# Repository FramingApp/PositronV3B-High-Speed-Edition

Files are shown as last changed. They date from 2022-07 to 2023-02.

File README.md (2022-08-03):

<p align="center">
   
</p>

---

# PositronV3**B**

<!-- [Check out our Youtube to see it in action!](https://www.youtube.com/watch?v=X_QLxTVtyng)

![alt text](https://github.com/KRLAYN/PositronV3/blob/main/Media%20and%20logos/Photos%20and%20renders/PV3%20with%20printsA.jpg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) -->

A modified version if the fantastic [PositronV3 Upside Down 3D Printer](https://github.com/KRLAYN/PositronV3).<br />
This version is deigned to be more manufacturable by hobbyists, with improoved performance (infact prints faster).
<br /><br />
**Features**
-  **No Machined Parts**, *except hotend*
-  **No Synchromesh**, *uses kevlar string*
-  Requires only Hand Hools and 3D printer
-  Integrated PSU

<br />

[BOM Link](https://docs.google.com/spreadsheets/d/1i8a5PYKq8QxL8bjgeb9Q3jwmtq4bS95erUoR0jqxsa8/edit?usp=sharing)

<br />

>**Disclaimer**: `Positron V3B` is still under heavy and rapid development, and things **will change**, if you find somthing that could be improoved, either submit a PR or an Issue in this Git page, or contact harryloud#8251 or AudiotroniX#0585 on Discord.

# Licenses



**License usage**: `CC-BY`

If you are manufacturing this 3D printer or a close derivative, please put `KRALYN Design Logo` visibily on your product and designate `KRALYN` as the inventor of this product. You can find the file inside the logos folder.

***All hardware materials and designs provided here are licensed under the [CC-BY-SA-4.0](https://creativecommons.org/licenses/by-sa/4.0/) hardware license.
All documentation, including the Wiki, is under the Creative Commons [CC-BY-SA-4.0](https://creativecommons.org/licenses/by-sa/4.0/) license***.

<div align="center">
Open Licenses
</div>

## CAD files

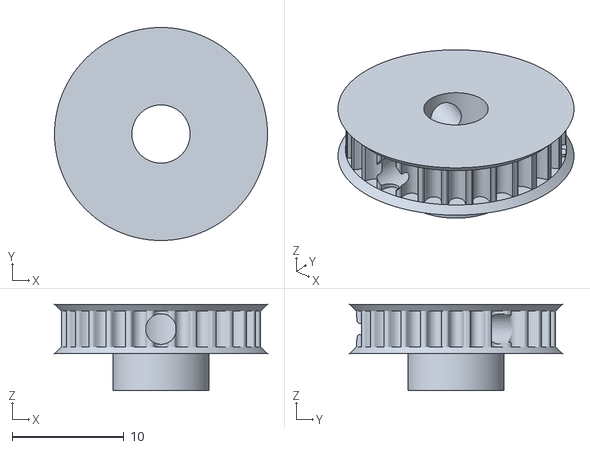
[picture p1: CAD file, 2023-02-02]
CAD files/NX/Pulley_T-MXL-XL-HTD-GT2_N-tooth.stl
19.0 x 19.0 x 7.70

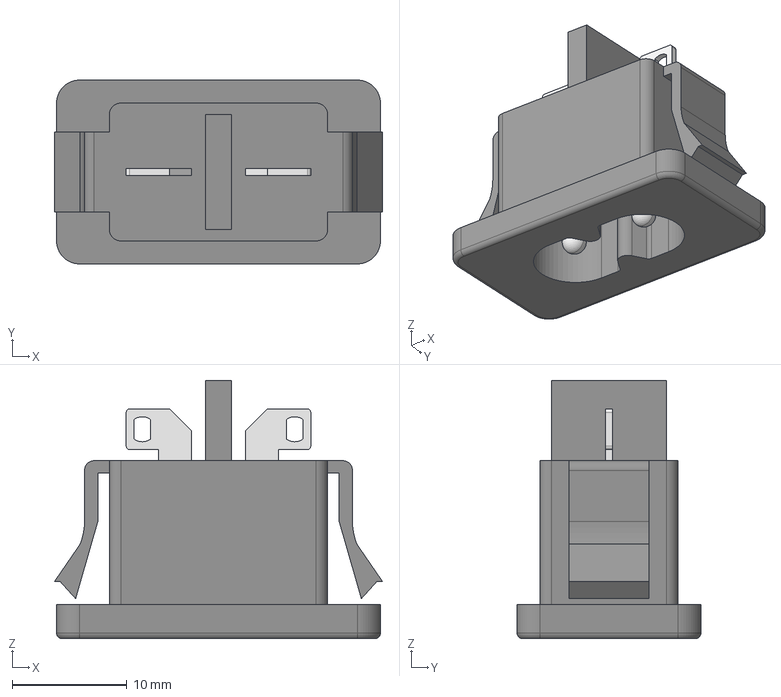
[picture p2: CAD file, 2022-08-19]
CAD files/NX/c7_plug-in.stp
28.6 x 16.0 x 22.5 mm

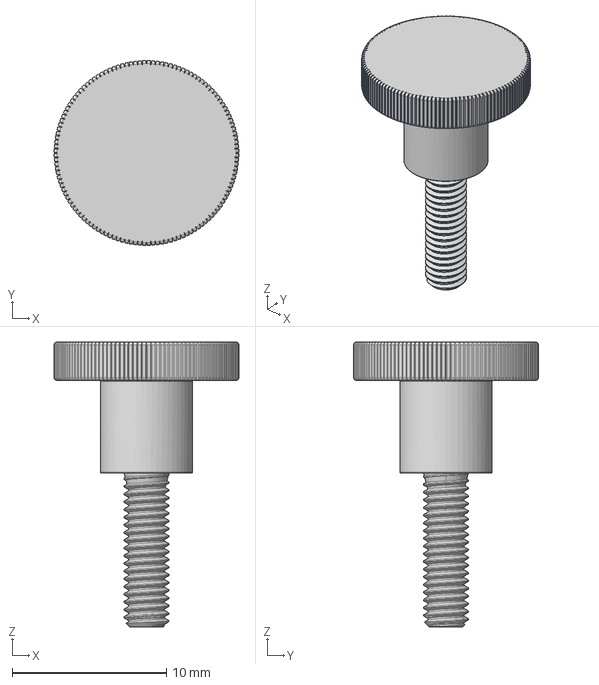
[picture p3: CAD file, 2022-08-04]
CAD files/NX/SKT-M3-10-A1 v1.step
12.0 x 12.0 x 18.5 mm

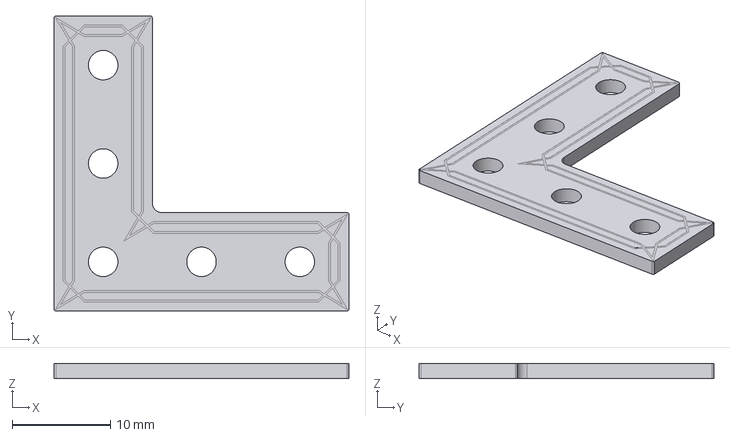
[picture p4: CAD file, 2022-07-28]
CAD files/NX/Makerbeam large right angle stainless bracket.stp
30.0 x 30.0 x 1.50 mm

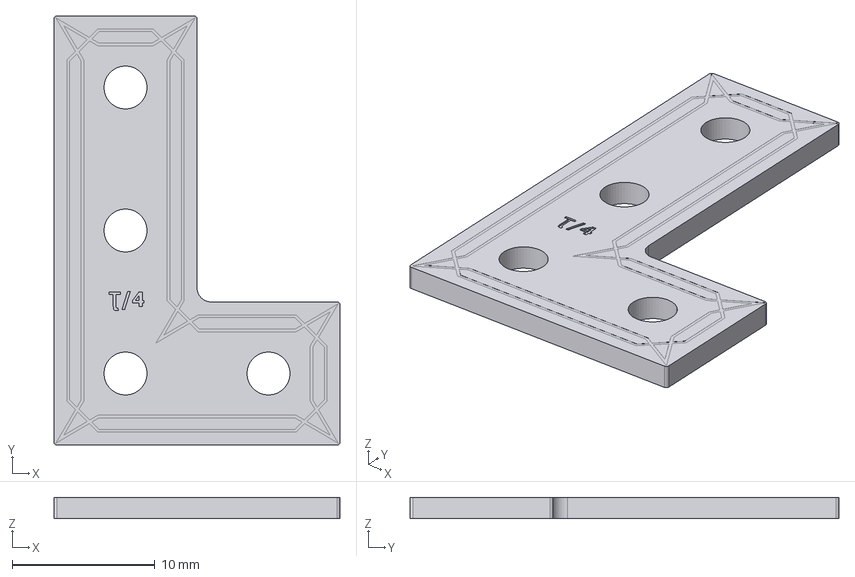
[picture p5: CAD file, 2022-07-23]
CAD files/NX/MakerbeamLBracket-100304.stp
20.0 x 30.0 x 1.50 mm

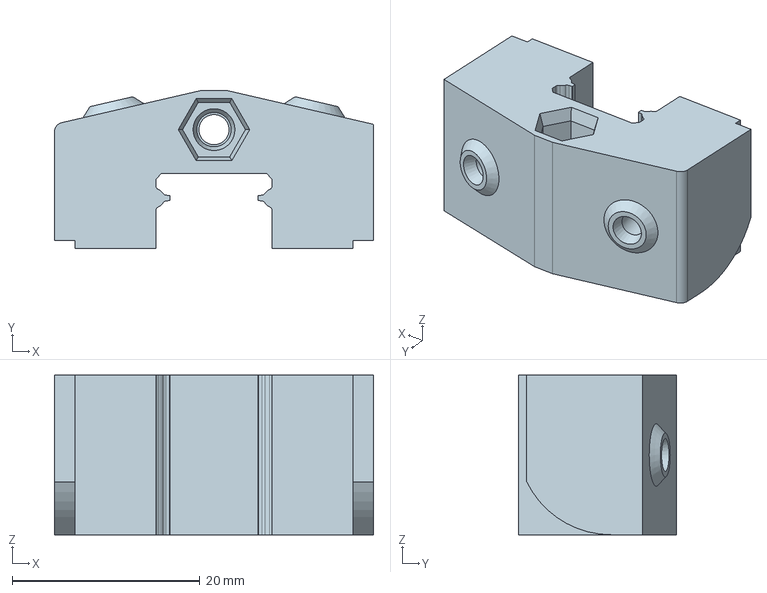
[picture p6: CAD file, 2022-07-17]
CAD files/NX/End Holder Block - Tensioning Mod, 1 part, moving ledges.stp
34.0 x 16.9 x 17.0 mm

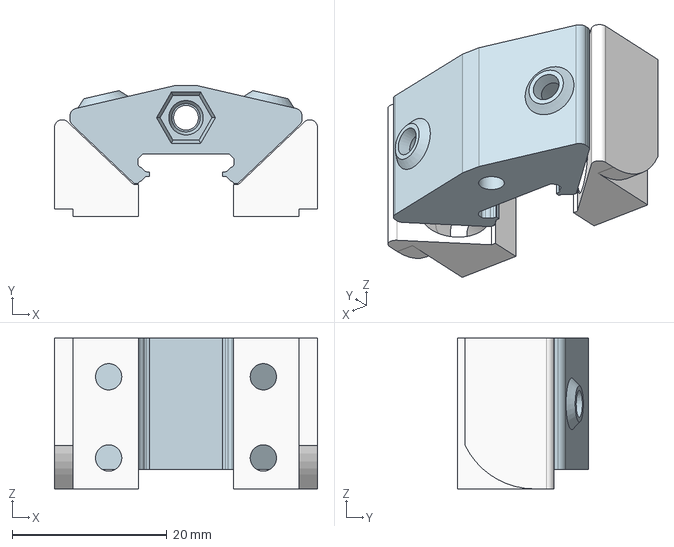
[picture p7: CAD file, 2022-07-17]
CAD files/NX/End Holder Block - Tensioning Mod, Fixed Ledges.stp
34.0 x 17.0 x 19.5 mm

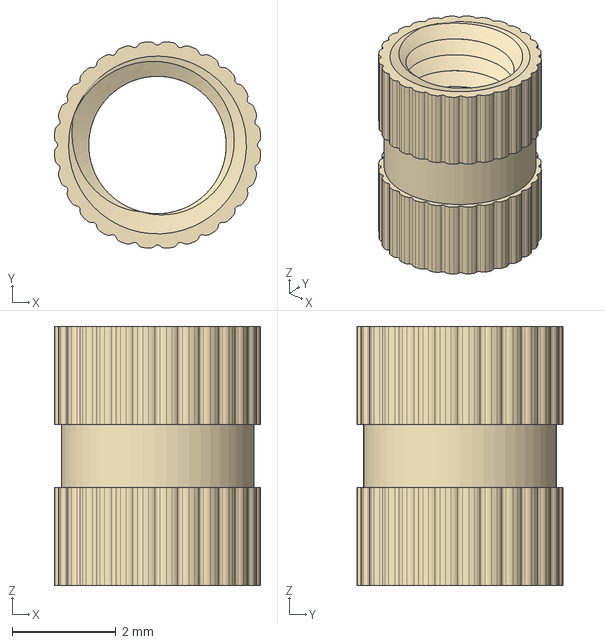
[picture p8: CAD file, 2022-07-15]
CAD files/NX/Threaded Insert - M3x5x4.stp
3.99 x 3.99 x 5.00 mm

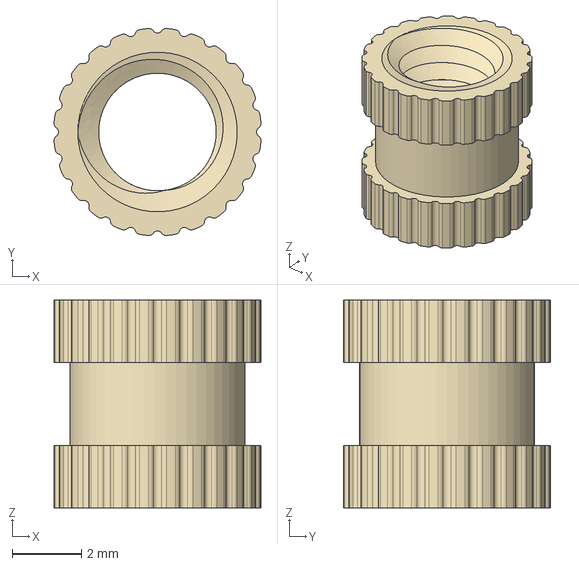
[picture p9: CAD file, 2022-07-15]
CAD files/NX/Threaded Insert - M4x6x6.stp
5.98 x 5.98 x 6.00 mm

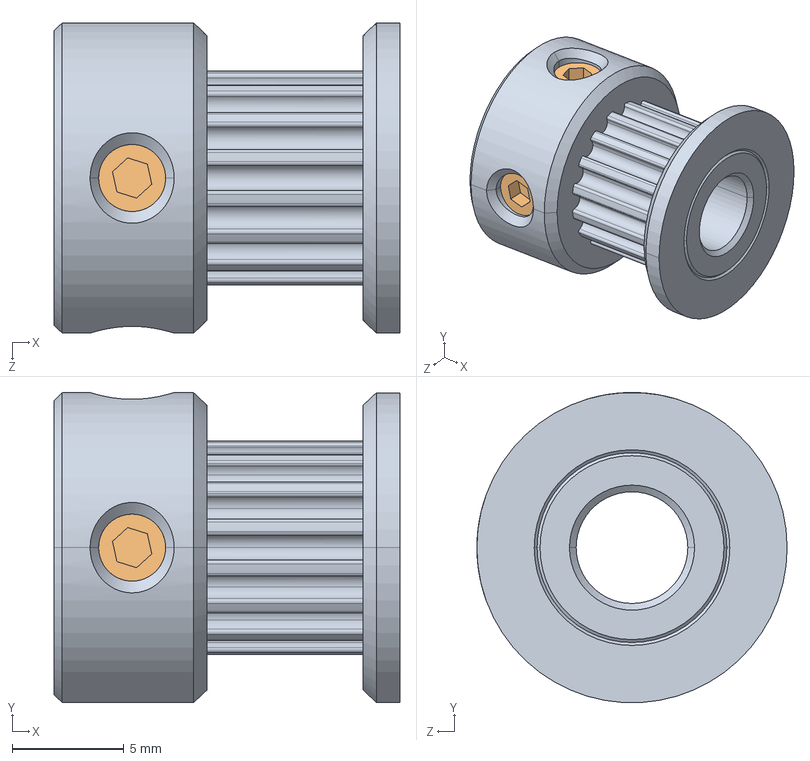
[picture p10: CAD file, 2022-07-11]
CAD files/NX/GT2_16T.STEP
15.5 x 13.9 x 13.9 mm

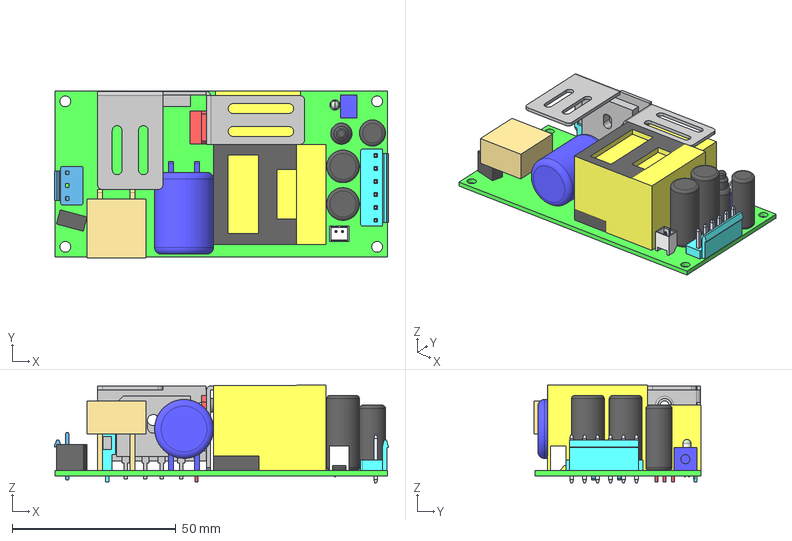
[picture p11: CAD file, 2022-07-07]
CAD files/NX/EPP-200.stp
102.0 x 51.1 x 29.8 mm
PCB
CN1
PIN_CPY
PIN_CPY_CPY
USER_LIBRARY-B5P-VH_PINVH x 6
USER_LIBRARY-B5P-VH_B5P-BODY_WH
C110
p2
pin.1.2.1
C105 x 2
t1
VR
L100
C5
C1
FS2
LED
P110I
BD1
Q1
T2

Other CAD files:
CAD files/NX/Makerbeam_T-Slot_Nut.step
CAD files/NX/Pulley_T-MXL-XL-HTD-GT2_N-tooth.scad
CAD files/1030 extruded aluminum.prt
CAD files/10Pin EXP Male.prt
CAD files/15mm pDia Syncromesh (Mirror).prt
CAD files/19.5mm pDia Syncromesh.prt
CAD files/3 pin 2.54.prt
CAD files/3.5TFT GPIO RPI.prt
CAD files/3.81mm syncromesh 19.81mm gear.prt
CAD files/30mm Fan Mockup 3010 v5.prt
CAD files/37mm 5mm Shaft.prt
CAD files/3D printed toolhead interconnect.prt
CAD files/3x8x15mm Al standoff.prt
CAD files/3x8x15mm Al standoff_1.prt
CAD files/3x8x9.5mm spacers.prt
CAD files/4x12mm Dowel pin.prt
CAD files/5.5mm M3spacors.prt
CAD files/5.5mm m3 Spacros.prt
CAD files/5542481392_step.prt
CAD files/5542484352_step.prt
CAD files/5ohm Polyester Film Heater 10x21cm.prt
CAD files/6 pin megnegtic Pogo Pins.prt
CAD files/6483370560.step_1.prt
CAD files/6483370560.step_2.prt
CAD files/6483370560.step_3.prt
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

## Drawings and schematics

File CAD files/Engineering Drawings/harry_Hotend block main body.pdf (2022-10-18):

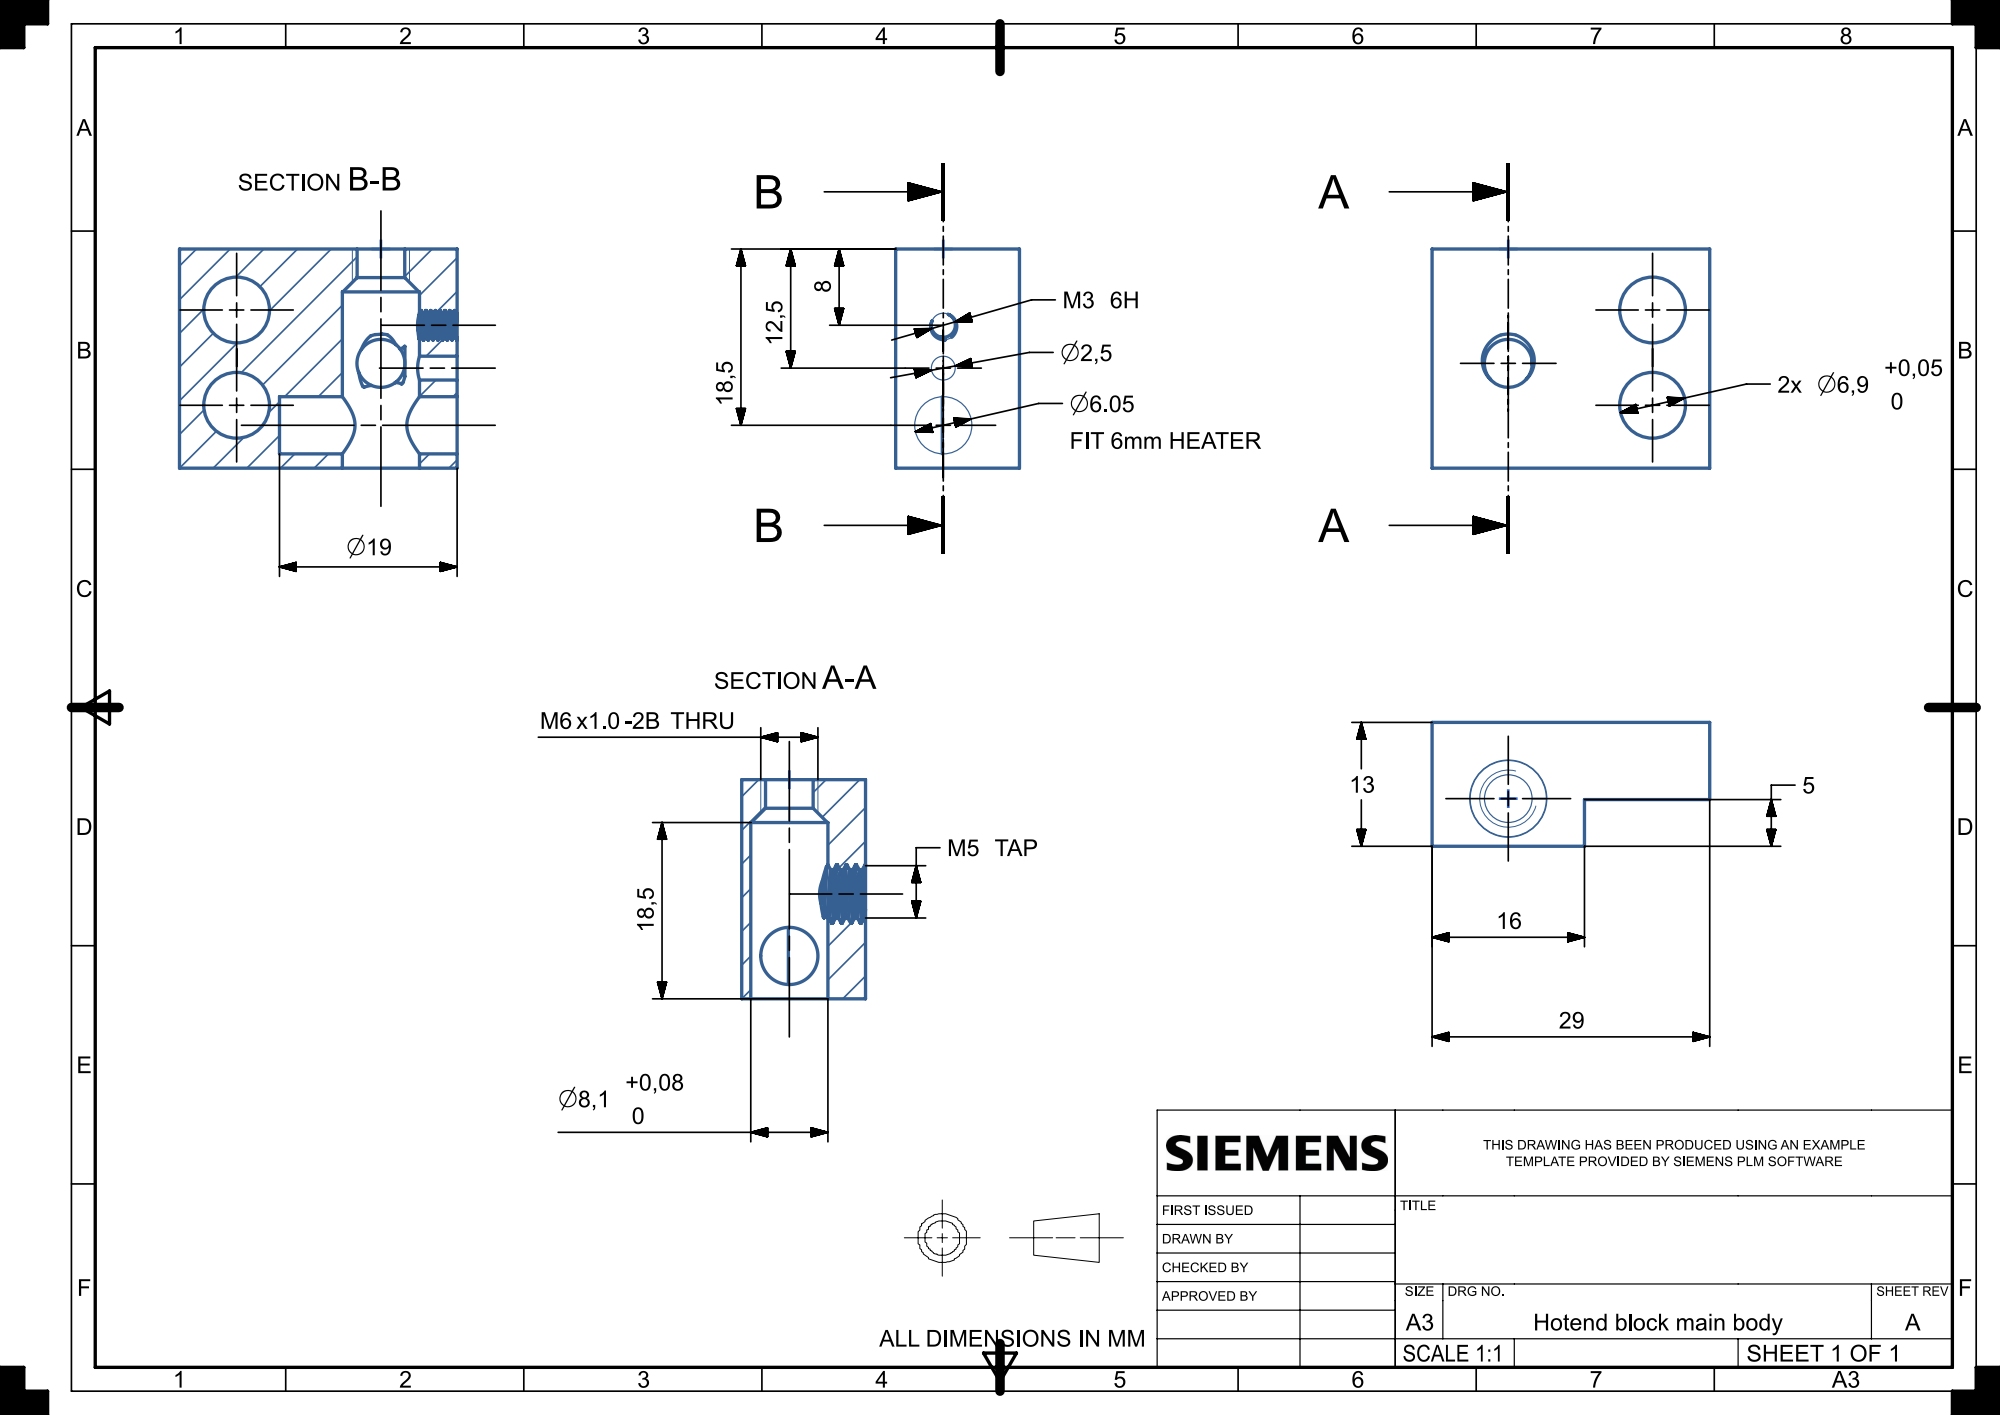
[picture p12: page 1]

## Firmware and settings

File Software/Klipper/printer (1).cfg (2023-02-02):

[printer]
kinematics: corexy
max_velocity: 350
max_accel: 8000
max_accel_to_decel: 7000
square_corner_velocity: 7
max_z_velocity: 7
max_z_accel: 100

[mcu]
serial: /dev/ttyS3
baud: 250000
restart_method: command

[mcu bpi]
serial: /tmp/klipper_host_mcu



[stepper_x] #ST4118X1404-A Motor
step_pin: gpio11
dir_pin: !gpio10
enable_pin: !gpio12
microsteps: 16 #Microsteps were found to improove max speed
rotation_distance: 58.1 #57.1 #set to 60 to run velocity in rpm
#endstop_pin: ^gpio3
endstop_pin: tmc2209_stepper_x:virtual_endstop
homing_retract_dist: 0
position_endstop: 0
position_max: 185
homing_speed: 40
full_steps_per_rotation: 200
step_pulse_duration: 0.000001 #helps with speed a bit
[tmc2209 stepper_x]
interpolate: false
uart_pin: gpio9
tx_pin: gpio8
uart_address: 0 # X = 0, Y = 2
run_current: 1.2 #1.4
#hold_current: 0.7
stealthchop_threshold: 250 #999999
diag_pin: ^gpio4 #x = gpio4, y = gpio3, z = gpio25
driver_SGTHRS: 21

[stepper_y]
step_pin: gpio6
dir_pin: !gpio5
enable_pin: !gpio7
microsteps: 16
rotation_distance: 58.1 #57.1
#endstop_pin: ^gpio4
endstop_pin: tmc2209_stepper_y:virtual_endstop
homing_retract_dist: 0
position_endstop: 0
position_max: 180
homing_speed: 40
full_steps_per_rotation: 200
step_pulse_duration: 0.000001
[tmc2209 stepper_y]
interpolate: false
uart_pin: gpio9
tx_pin: gpio8
uart_address: 2 # X = 0, Y = 2
run_current: 1.2 #1.4
#hold_current: 0.7
stealthchop_threshold: 250 ;999999
diag_pin: ^gpio3 #x = gpio4, y = gpio3, z = gpio25
driver_SGTHRS: 24


[stepper_z]
step_pin: gpio19
dir_pin: gpio28
enable_pin: !gpio2
microsteps: 16
rotation_distance: 4 #lead screw pitch
endstop_pin: probe:z_virtual_endstop
position_min: -2.0
position_max: 181
homing_speed: 12

[tmc2209 stepper_z]
uart_pin: gpio9
tx_pin: gpio8
uart_address: 1
run_current: 0.7
hold_current: 0.4
stealthchop_threshold: 999999

[extruder]
step_pin: gpio14 #gpio19
dir_pin: !gpio13 #gpio28
enable_pin: !gpio15 #!gpio2
microsteps: 16
rotation_distance: 4.92#1.65
nozzle_diameter: 0.6
filament_diameter: 1.75
full_steps_per_rotation: 400 #0.9 deg
heater_pin: gpio23
sensor_type: Generic 3950
sensor_pin: gpio27
control: pid
pid_Kp: 25.12
pid_Ki: 1.073
pid_Kd: 147
min_temp: -100
max_temp: 255
max_extrude_cross_section:2
pressure_advance: 0.18 #0.18
min_extrude_temp: 170
max_extrude_only_distance: 1000

[tmc2209 extruder]
uart_pin: gpio9
tx_pin: gpio8
uart_address: 3 #1
run_current: 0.7#0.69
hold_current: 0.4#0.4
stealthchop_threshold: 999999

[heater_bed]
heater_pin: gpio21
sensor_type: Generic 3950
sensor_pin: gpio26
pwm_cycle_time: 0.3#0.015 #longer as small electric shock when touching ITO. Hurts if high freqency
max_power: 1
control: pid
pid_Kp: 56.852
pid_Ki: 2.1
pid_Kd: 383.75
min_temp: -100
max_temp: 90

[controller_fan mcu_fan]
pin: gpio18
max_power: 1
shutdown_speed: 0
cycle_time: 0.00002
kick_start_time: 1
fan_speed: 1
idle_timeout: 1
stepper: stepper_x, stepper_y#, stepper_z


# [heater_fan nozzle_cooling_fan]
# pin: gpio20
# kick_start_time: 1

[fan]
pin: gpio20#bpi:gpiochip0/gpio17
max_power: 1
cycle_time: 0.001 #https://www.youtube.com/watch?v=E3kBau82SwU&ab_channel=Vez3D
hardware_pwm: false
shutdown_speed: 0
#pin: gpio18
# kick_start_time: 1


[heater_fan extruder_heatsink_fan]
heater: extruder
heater_temp: 50.0
pin: gpio17
max_power: 1
shutdown_speed: 0
cycle_time: 0.00002
# kick_start_time: 1
fan_speed: 1
# idle_timeout: 5






[force_move]
enable_force_move = true

[gcode_macro FORCE_Z_UP]
gcode: FORCE_MOVE STEPPER=stepper_z DISTANCE=30 VELOCITY=40

[virtual_sdcard]
path: ~/gcode_files

[safe_z_home]
home_xy_position: 90,90 #90,90 # Change coordinates to the center of your print bed
speed: 100
z_hop: 3                # Move up 5mm
z_hop_speed: 5

[probe]
pin: ^gpio25 #x = gpio4, y = gpio3, z = gpio25
x_offset: -6
y_offset: -40
#z_offset: 1.5 #0.8
speed: 3
samples: 3
sample_retract_dist: 0.7

[bed_tilt]
points: 
  25,15
  130,15
  130,150
  35,150
speed: 100
horizontal_move_z: 4

[bed_screws]
screw1: 0, 145
screw2: 170, 145
screw3: 100, 0




[gcode_macro UNLOAD_FILAMENT]
gcode = 
  M83 
  G1 E-30 F1800
  G1 E-300 F2500 #880
  # G1 E-100 F1200
  # G1 E-100 F1200
  # G1 E-100 F1200
  G92 E0
  G90

[gcode_macro LOAD_FILAMENT]
gcode = 
  M83 
  G1 E300 F2500 #300
  # G1 E100 F1200
  # G1 E100 F1200
  # G1 E100 F1200
  G1 E20 F600
  G92 E0
  G90
  



[gcode_macro G29]
gcode = 
  G28
  G1 Z5 F800
	BED_TILT_CALIBRATE

[delayed_gcode my_delayed_gcode]
gcode:
    SET_LED LED=WS2812 RED=0 GREEN=0.05 BLUE=0.01 INDEX=3
    SET_LED LED=WS2812 RED=0.1 GREEN=0.1 BLUE=0.05 INDEX=2
    SET_LED LED=WS2812 RED=0.1 GREEN=0.1 BLUE=0.05 INDEX=1
    G4 P100
    SET_LED LED=WS2812 RED=0 GREEN=0.1 BLUE=0.02 INDEX=3
    SET_LED LED=WS2812 RED=0.2 GREEN=0.2 BLUE=0.1 INDEX=2
    SET_LED LED=WS2812 RED=0.2 GREEN=0.2 BLUE=0.1 INDEX=1
    G4 P100
    SET_LED LED=WS2812 RED=0 GREEN=0.15 BLUE=0.04 INDEX=3
    SET_LED LED=WS2812 RED=0.3 GREEN=0.3 BLUE=0.15 INDEX=2
    SET_LED LED=WS2812 RED=0.3 GREEN=0.3 BLUE=0.15 INDEX=1
    G4 P100
    SET_LED LED=WS2812 RED=0 GREEN=0.2 BLUE=0.05 INDEX=3
    SET_LED LED=WS2812 RED=0.4 GREEN=0.4 BLUE=0.2 INDEX=2
    SET_LED LED=WS2812 RED=0.4 GREEN=0.4 BLUE=0.2 INDEX=1
    G4 P100
    SET_LED LED=WS2812 RED=0 GREEN=0.3 BLUE=0.1 INDEX=3
    SET_LED LED=WS2812 RED=0.5 GREEN=0.5 BLUE=0.25 INDEX=2
    SET_LED LED=WS2812 RED=0.5 GREEN=0.5 BLUE=0.25 INDEX=1
    G4 P100
    SET_LED LED=WS2812 RED=0.6 GREEN=0.6 BLUE=0.3 INDEX=2
    SET_LED LED=WS2812 RED=0.6 GREEN=0.6 BLUE=0.3 INDEX=1
    G4 P100
    SET_LED LED=WS2812 RED=0.7 GREEN=0.7 BLUE=0.35 INDEX=2
    SET_LED LED=WS2812 RED=0.7 GREEN=0.7 BLUE=0.35 INDEX=1
    G4 P100
    SET_LED LED=WS2812 RED=0.9 GREEN=0.9 BLUE=0.45 INDEX=2
    SET_LED LED=WS2812 RED=0.9 GREEN=0.9 BLUE=0.45 INDEX=1
initial_duration: 0.1

[pause_resume]

[gcode_macro CANCEL_PRINT]
rename_existing: BASE_CANCEL_PRINT
gcode:
  TURN_OFF_HEATERS
  CLEAR_PAUSE
  SDCARD_RESET_FILE
  G91 E0
  G1 E-1.0 F240
  G92 E0
  G1 X5 Y5 F3000
  G91
  G1 Z25 F800
  G1 Z25 F800
  G1 Z25 F800
  G90

  BASE_CANCEL_PRINT

[gcode_macro RESUME]
rename_existing: BASE_RESUME
gcode:
  ##### read E from pause macro #####
  {% set E = printer["gcode_macro PAUSE"].extrude|float %}
  ##### end of definitions #####
  G91
  G1 E{E} F240
  RESTORE_GCODE_STATE NAME=PAUSE_state
  BASE_RESUME

[gcode_macro PAUSE]
rename_existing: BASE_PAUSE
# change this if you need more or less extrusion
variable_extrude: 1.0
gcode:
  ##### read E from pause macro #####
  {% set E = printer["gcode_macro PAUSE"].extrude|float %}
  ##### set park positon for x and y #####
  # default is your max posion from your printer.cfg
  {% set x_park = printer.toolhead.axis_maximum.x|float - 10.0 %}
  {% set y_park = printer.toolhead.axis_maximum.y|float - 10.0 %}
  ##### calculate save lift position #####
  {% set max_z = printer.toolhead.axis_maximum.z|float %}
  {% set act_z = printer.toolhead.position.z|float %}
  {% if act_z < (max_z - 2.0) %}
      {% set z_safe = 2.0 %}
  {% else %}
      {% set z_safe = max_z - act_z %}
  {% endif %}
  ##### end of definitions #####
  SAVE_GCODE_STATE NAME=PAUSE_state
  BASE_PAUSE
  G91
  G1 E-{E} F240
  G1 Z{z_safe} F900
  G90
  G1 X{x_park} Y{y_park} F5000



[gcode_macro BACK_AND_FORTH_X_TIMES]
gcode: 
  {% set numtimes = params.NUMTIMES|default(1, true)|int %}
  {% set motor_letter = params.MOTOR_LETTER|default("x", true)|string %}
  {% set speed = params.SPEED|default(500, true)|int %}
  {% set accel = params.ACCEL|default(10000, true)|int %}

  {% for i in range(numtimes * 2) %}
    FORCE_MOVE STEPPER=stepper_{ motor_letter } DISTANCE={ "-" if (i%2 == 1) }200 VELOCITY={ speed } ACCEL={ accel } 
  {% endfor %}



[neopixel WS2812]
pin: gpio24
chain_count: 5
color_order: GRB
initial_RED: 0.0
initial_GREEN: 0.0
initial_BLUE: 0.0

[display_status]

#*# <---------------------- SAVE_CONFIG ---------------------->
#*# DO NOT EDIT THIS BLOCK OR BELOW. The contents are auto-generated.
#*#
#*# [bed_tilt]
#*# x_adjust = 0.006243
#*# y_adjust = -0.013471
#*# z_adjust = 0.186993
#*#
#*# [probe]
#*# z_offset = 1.700

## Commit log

2022-05-24 initial pissings about of bldc with a MAD 5005 with 4:1 reduction
    [1030 extruded aluminum.prt, 10Pin EXP Male.prt, 15mm pDia Syncromesh (Mirror).prt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]
2022-05-25 NX: Laoded in a work started on modifying baseplate and integrating components
    [1030 extruded aluminum.prt, 10Pin EXP Male.prt, 15mm pDia Syncromesh (Mirror).prt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]
2022-07-04 Extruder angled to allow the fillament path to go behind the z axis. This eliminates the need to cut a large slot in the z axis.
    The z axis has also been converted to use 10x10 makerbeam extrusions
    [1030 extruded aluminum.prt, AL bracket Extruder Mounting.prt, Extruder Cap.prt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]
2022-07-07 Figuring out layout of motors and boards. Z axis leadscrew currently uses a needle bearing, but probalby move to deep groove beraings
    [03-26000.prt, 06-8_A.prt, 1030 extruded aluminum.prt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]
2022-07-11 Was thinking about using flanged ball bearings, and removable belt from the z axis pulley.
    However it woudl be better to have a spring loaded z motor and captive belt ont eh z pulley adn stow the pulley around the back of the z axis when in storage. ANd move back to needle bearings
    [90 degree Bed Holder.prt, Base Plate.prt, Base plate and Y axis assembly.prt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]
2022-07-15 Z axis block modifed for 3d printing, required a m4 and m3 insert. Also tensions from hte z block now. Much better. I have 3d pritned and tested and appears to work well.
    [90 degree Bed Holder.prt, Base plate and Y axis assembly.prt, MGW 9 Rail v1.prt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]
2022-07-15 Modifed Z axis holder block to use captive nut as m3 insert kept pulling out according to MellonColley's discord testing. Also added supressed modifcation to Z axis block that enables it for use on t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
    [Z axis Holder block.prt]
2022-07-15 Working paarametic Pulley. Collar is designed to fit down, through the motor throat and sit agianst the bearing for perfect height.
    Print at 0.1mm, 100% infil and with a brim or raft if havign trouble printing
    [synchromeshPulleyNXAttempt.prt]
2022-07-17 After Testing of the tnesioning end holder block mod by MelonColley, some updates were done. 1st, it allows the use of either a m3 insert, or a m3 nut. And 2nd, 2 versions have been created. One is a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
    This is not mature and ready for a PR to the main postron repo.
    [End Holder Block - Tensioning Mod, 1 part, moving ledges.stp, End Holder Block - Tensioning Mod, Fixed Ledges.stp, Z axis Holder block.prt]
2022-07-17 Genral Updates, Pulleys modifed for 28mm motors, Bed hodler updated further for 3d printing. Z axis lead screw and top stopper have been printed and tested in real life and small modifications have b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
    [90 degree Bed Holder.prt, Nema 17 28mm.prt, Positron V3.2 Rev B UNFOLEDE v53_step.prt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]
2022-07-23 Lots and lots of improovments from 3d printing testing. Figured out the placement of electronics (PSU Left 2 arrangment). XY Motor active cooling done via 2 fans and a 22x70x6mm SSD heatsink that has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
    Positioning of components, especialy the fan became very diffuclt in the folded position. As such, the printer base may have to be extended by 2mm.
    Might move to 26.5mm E3D ste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
    [1030 extruded aluminum.prt, 10Pin EXP Male.prt, 14x5x5mm bearing.prt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]
2022-07-27 After testing, it was found that the fit of the leadscnut was far too constrained.
    There was also significant flex when bending downwards.
    To solve this, steel L brackets will be added similar to the z block.
    The magnetic pin/ bed position may also be lowered to allow the overall thickning of the plastic parts that hold the arms, and intergration of the top 2 screws into it for even more stifness.
    This lowering will reduce the z movement by 5-10mm, but its worth it.
    There was also noticable side to side wiggle of the arms in their socket.
    This will be because of no constrainment by the screwed top bit, so a wedge will be put in place to attempt to constrain their side to side motion better.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
    [90 degree Bed Holder.prt]
2022-07-27 V3 of 90 deg bed holder.
    Bed mounting moved 8.75mm lower, thus everything much thicker, and should be sturdier.
    Simulation showed this reduced bending from 10 - ~4mm (100N), which is a massive improovment.
    https://www.simscale.com/projects/harryloud/bending_again/ (V3)
    Next to integrate some stainless steel makerbeam brackets to stiffen furhter and also raise the height of the Z block (and change to the larger bracket size).
    [90 degree Bed Holder.prt, BedArmExtrusion_00.prt, BedArmExtrusion_01.prt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]
2022-07-28 Z Block & 90 deg bed holder tested and stable.
    Stainless bracket installed in the 90 deg bed holder for improoved stifness.
    Simulation showed this reduced bending from 4mm - ~2.8mm (100N), which is an improovment on v3.
    So essentialy its just the extrusion arms that bend now, the 90 degree holder is ridgid.
    https://www.simscale.com/projects/harryloud/bending_again/ (V4)
    This part is complete and can move to enclosure design.
    Am thinking about placing the blower fan on the z extrusion, the otehr side of the extruder (leadscrew side) and use long brackets to hold it firm.
    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
    [Bed holder Optimized.prt, BedArmExtrusion_00.prt, BedArmExtrusion_01.prt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]
2022-08-01 Minor improovments with tollerances, smoothed thumb pusshing sport of 90 degree bed holder etc
    [Base Plate.prt, Nema 17 holder M3_1.prt, PRODUCT_NAME_10.prt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]
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2022-08-04 PSU housing, front motor mount and Z motor mount (Left side of printer), has been "completed", and testing will comence.
    Z motor mount:
    Initial idea was to use a thumb screw to fix the motor in place and rotate the entire motor to relaease adn tension the z belt.
    However, at the last miniute, asn alternative swinign idler design, infludenced by Krayalins origional z belt tensioner is beeing tested alongside as a replacement/similfication, and will likley be better.
    PSU Enclosure:
    Current number of slots for cooling may be too much, and testing will be required to see if it is adequite for convective cooling. And convesley, there may be too many slots for the forced air coolign fan to work,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
    [1030 extruded aluminum.step, 15mm pDia Syncromesh (Mirror).prt, 90 degree angled aluminum.step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]
2022-08-05 Minor Changes, + CFD of natural convection of base plate done. Data analysis now. Done on FLOEFD virsual pc online
    [Left Motor Assembly Rev A.prt, Nema 17 holder M3_1.prt, Positron V3.2 Rev B UNFOLEDE v53_step.prt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]
2022-08-19 Left side of positron mostly complete. Printed and tested.
    Z belt tensioner works orgasmicaly well
    [Base plate and Y axis assembly.prt, Left Motor Assembly Rev A.prt, Nema 17 holder M3_1.prt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]
2022-08-19 Bed heat transfer in free convection moddled in FEA (NX online FLOEFD). 85c isothermal plate, measuing the heat trasnfer per unit area. See results in plot.py in exported85cdata. Likley needs smoothi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
    [200x200x3mmbed.SLDPRT, exported-data-higher-density.csv, exported-data-higher-density.xlsx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]
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2022-08-27 RIGHT SIDE OF BASE DONE.
    Walls do need to be made a bit thinner tho to save on plastic and give a bit more space.
    [3.5TFT GPIO RPI.prt, Base plate and Y axis assembly.prt, KL Logo KRALYN Design CAD v1_step.prt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]
2022-09-24 Thinned the right side walls and cieling. Opened up the xy motor cable holes.
    [Positron V3.2 Rev B UNFOLEDE v53_step.prt]
2022-09-26 Added option (supressed), for external psu input and switch on left hand side.
    [Base plate and Y axis assembly.prt, Positron V3.2 Rev B UNFOLEDE v53_step.prt]
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2022-10-18 Improovments to Extruder. Change pulleys to use kevlar cord. Finalisation of Ducting/Hotend Pritned Part.
    Heatsinkless hotend was tried. It failed. Was not able to effectively insulate the heatblock from the x carriage, as such it got hot. + small ammount of heatscreep inside bowden tube.
    Will move to modified normal heatsink.
    Top lowered by 0.6mm to give more clearance to the x pulleys
    [Base plate and Y axis assembly.prt, Extruder Base.prt, Extruder Cap.prt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]
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2023-02-02 Angled extruder mild fix
    [AL bracket Extruder Mounting.prt, Extruder Base.prt, Extruder Mid body.prt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]
